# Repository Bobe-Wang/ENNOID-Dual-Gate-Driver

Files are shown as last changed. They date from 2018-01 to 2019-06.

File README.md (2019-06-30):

# ENNOID - Dual Gate Driver

The "Dual Gate Driver" can be directly connected to this control board:

https://github.com/paltatech/VESC-controller

The driver is pin compatible with several power modules such as the ones listed below:

- http://www.mitsubishielectric.com/semiconductors/content/product/powermod/powmod/igbtmod/tgatef/cm300du-12f_e.pdf
- https://www.wolfspeed.com/cas120m12bm2

## V0.1 (untested & archived):

V0.1 is based upon the design from wolfspeed two-channel gate driver for 1200V SiC MOSFET power modules
- https://www.wolfspeed.com/cgd15hb62p1

Feature:

- Dual gate driver
- 2W Isolated power supply / gate
- Direct mount low inductance design
- Short circuit protection
- Under voltage protection

Changes from the original wolfspeed design:

- Added Voltage sense circuit (Experimental)
- 98 x 60 mm 2 layer PCB made with Kicad
- Current sensor connector
- Temperature sensor circuit & connector
- Minimum SMD 0805 components size for easy handsoldering
- 2x8 (16) pins headers for easy connection with VESC board

## V0.2:

V0.2 is based upon the design from tiduc70a.pdf.

- http://www.ti.com/lit/ug/tiduc70a/tiduc70a.pdf

Changes from V0.1 include:

- BJT based powerstage instead of mosfet IC IXD-609
- Adjustable soft turnoff feature
- SMD gate resistor instead of MELF
- Active clamping / Over voltage protection
- Shoot trough EMI protection on PWM input

BOM link for 3 boards at Mouser below : 
- https://www.mouser.com/ProjectManager/ProjectDetail.aspx?AccessID=f6574b98ce

### Schematics

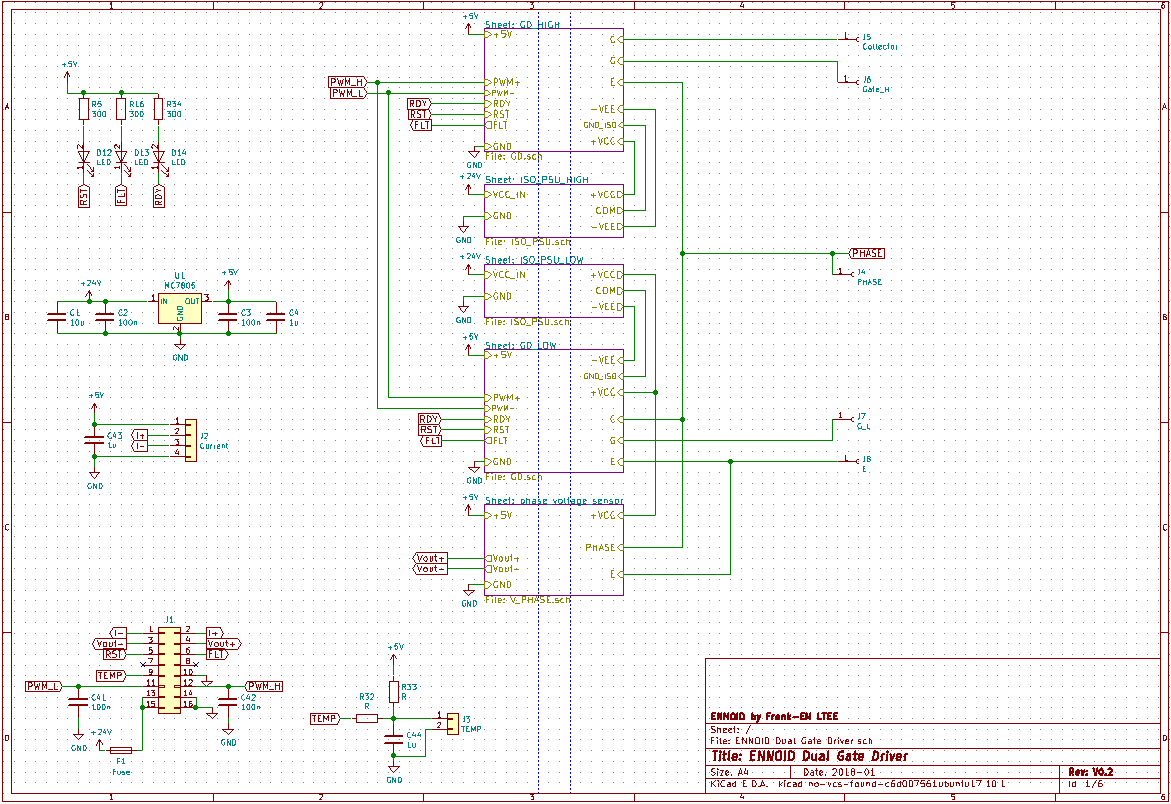
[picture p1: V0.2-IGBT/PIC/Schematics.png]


### Top View

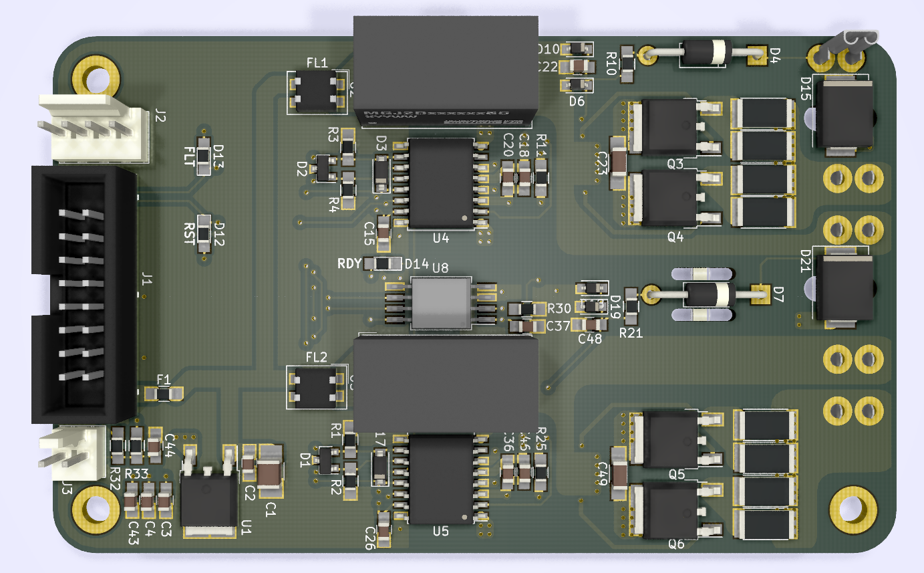
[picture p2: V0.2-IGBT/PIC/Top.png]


### Bottom View

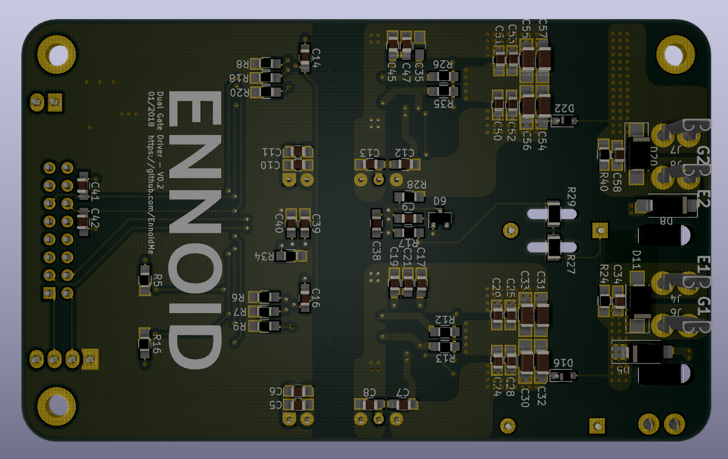
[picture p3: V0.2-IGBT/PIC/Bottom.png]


### Board View

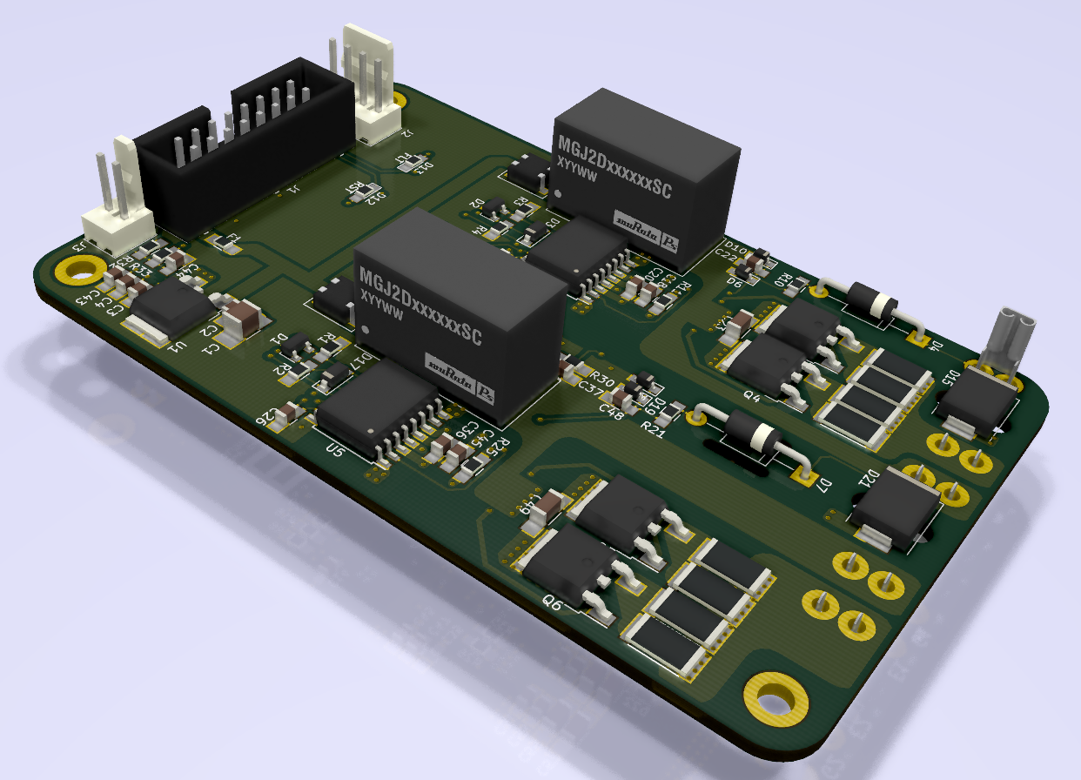
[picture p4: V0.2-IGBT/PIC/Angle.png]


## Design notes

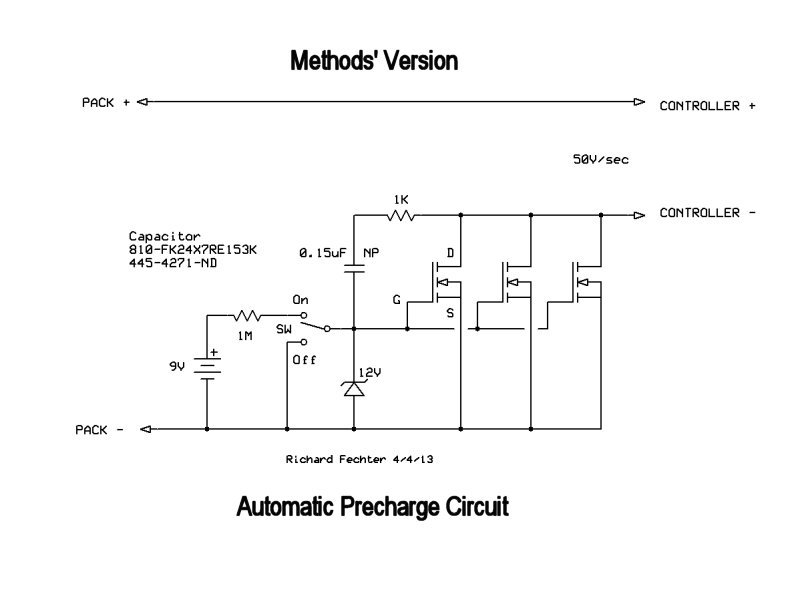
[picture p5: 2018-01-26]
VBUS-Sense/PCB/Automatic Precharge.jpg

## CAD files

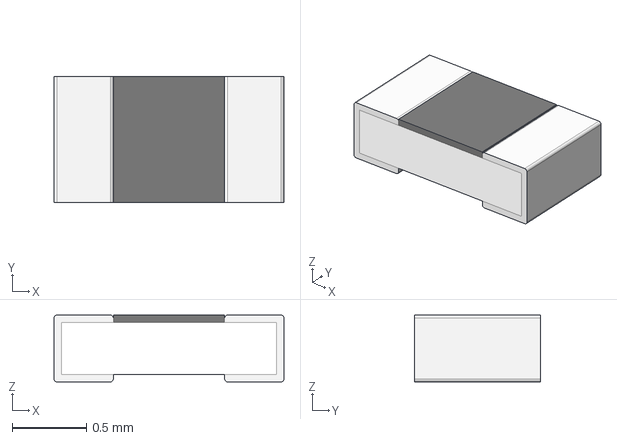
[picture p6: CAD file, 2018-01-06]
VBUS-Sense/3Dlib/r_0603_h078.step
1.55 x 0.85 x 0.45 mm

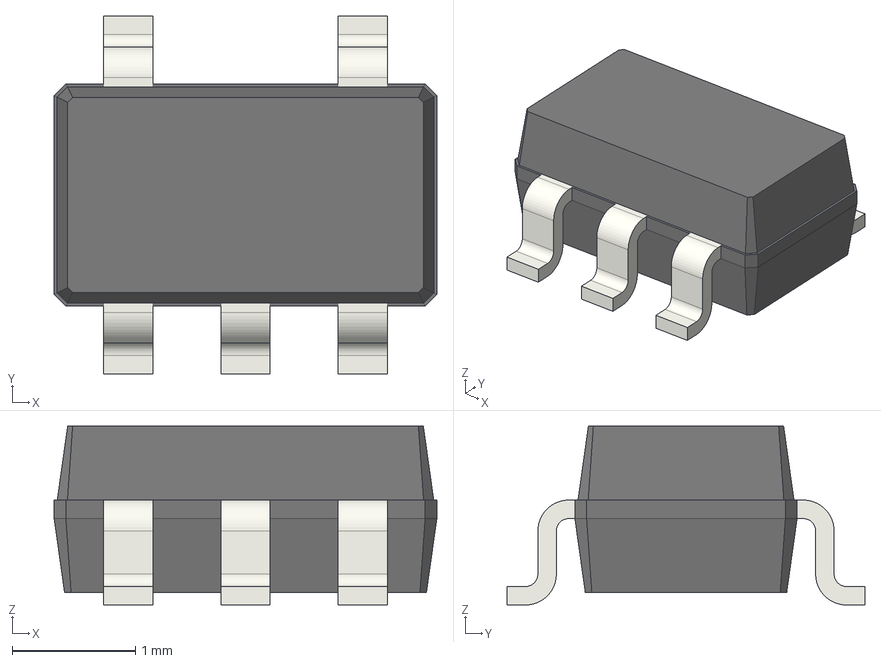
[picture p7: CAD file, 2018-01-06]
VBUS-Sense/3Dlib/sot23_5_18x29_p095.step
3.10 x 2.90 x 1.45 mm

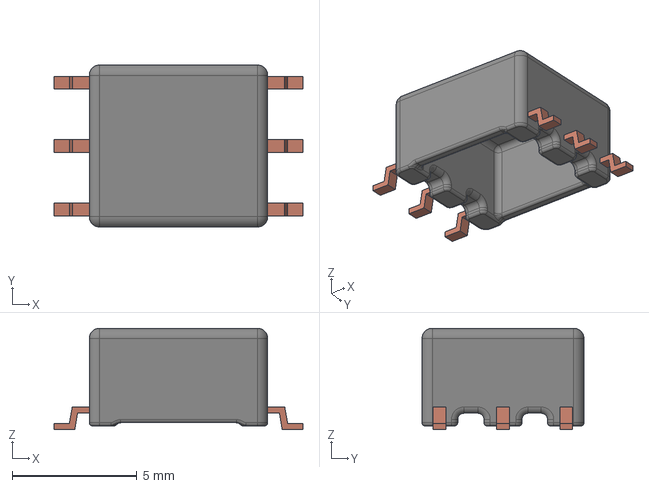
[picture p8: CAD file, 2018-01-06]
VBUS-Sense/3Dlib/250-1109-rev1.step
9.96 x 6.48 x 4.06 mm

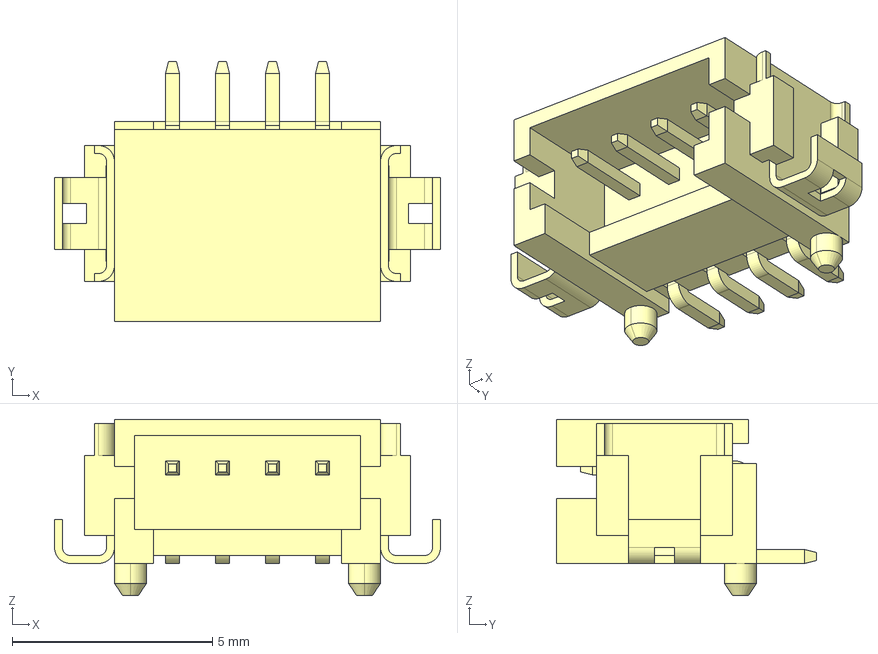
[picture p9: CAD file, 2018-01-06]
VBUS-Sense/3Dlib/DF13-4P-1.25H.stp
9.65 x 6.50 x 4.40 mm

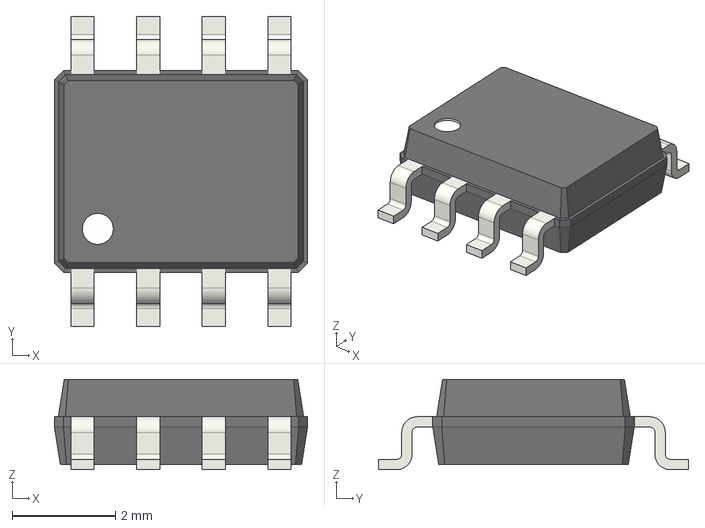
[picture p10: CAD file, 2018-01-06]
VBUS-Sense/3Dlib/soic_8_39x49_p127.step
4.90 x 6.00 x 1.75 mm

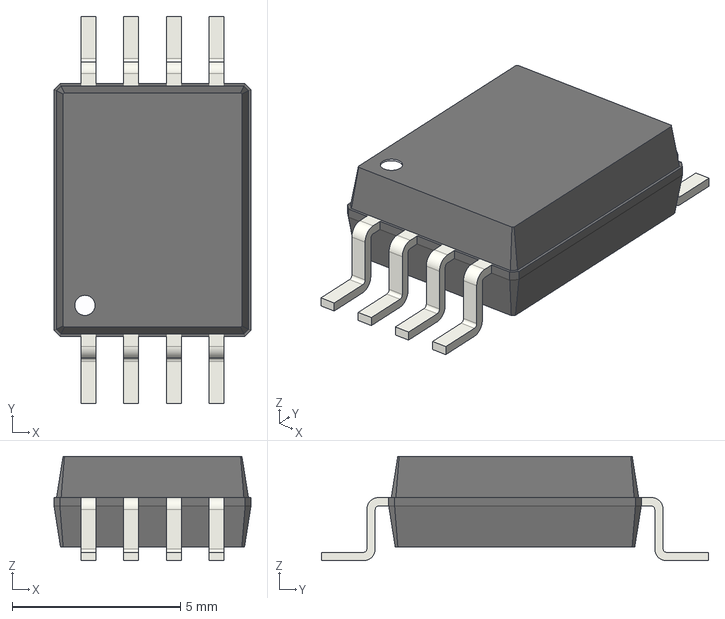
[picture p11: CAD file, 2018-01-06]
VBUS-Sense/3Dlib/soic_8_75x58_p127.step
5.85 x 11.5 x 3.10 mm

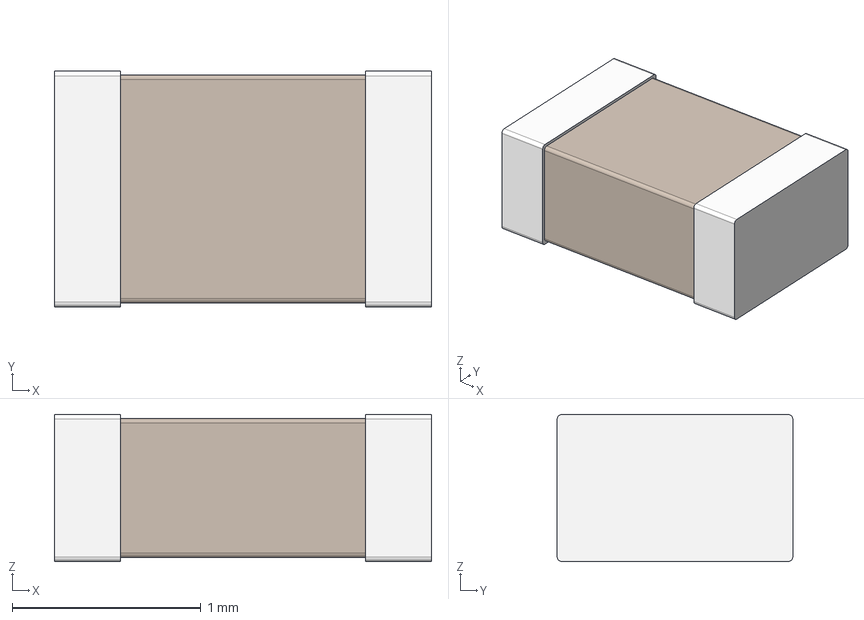
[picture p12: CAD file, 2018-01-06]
VBUS-Sense/3Dlib/c_0805_h078.step
2.00 x 1.25 x 0.78 mm

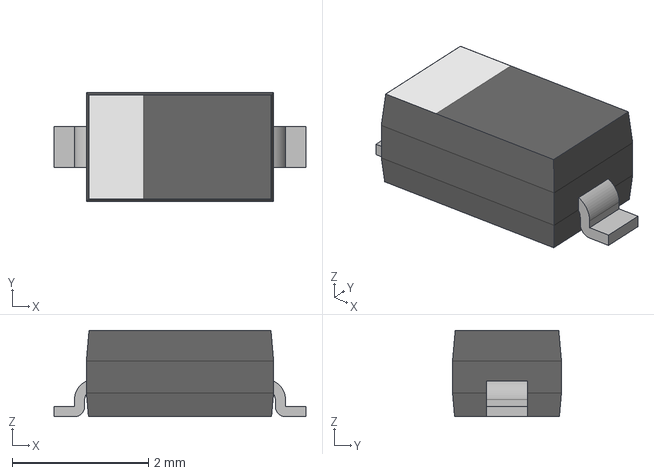
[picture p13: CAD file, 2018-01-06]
VBUS-Sense/3Dlib/SOD-123.step
3.70 x 1.60 x 1.27 mm

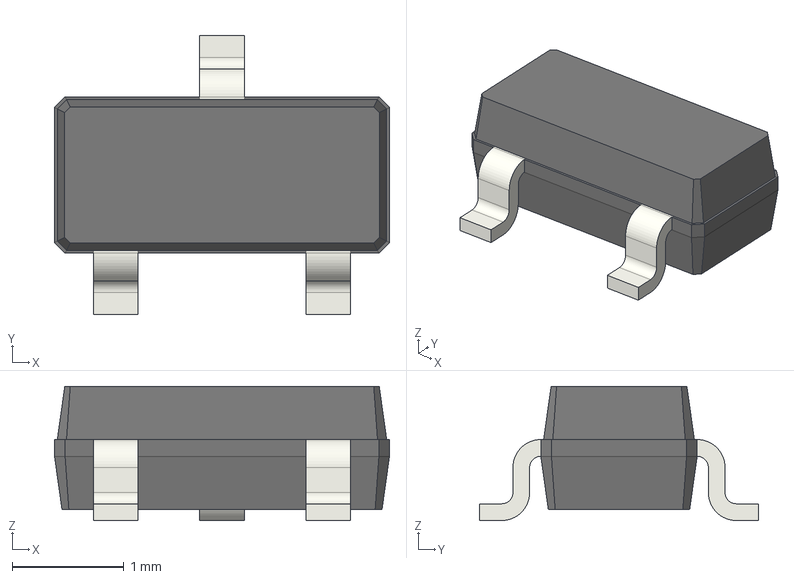
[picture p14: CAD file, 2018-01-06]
VBUS-Sense/3Dlib/sot23_3_25x30_p095.step
3.00 x 2.50 x 1.20 mm

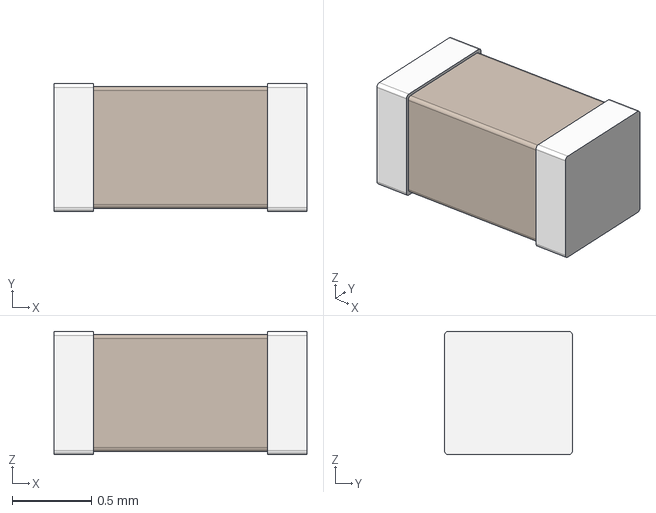
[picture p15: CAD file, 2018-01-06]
VBUS-Sense/3Dlib/c_0603_h078.step
1.60 x 0.81 x 0.78 mm

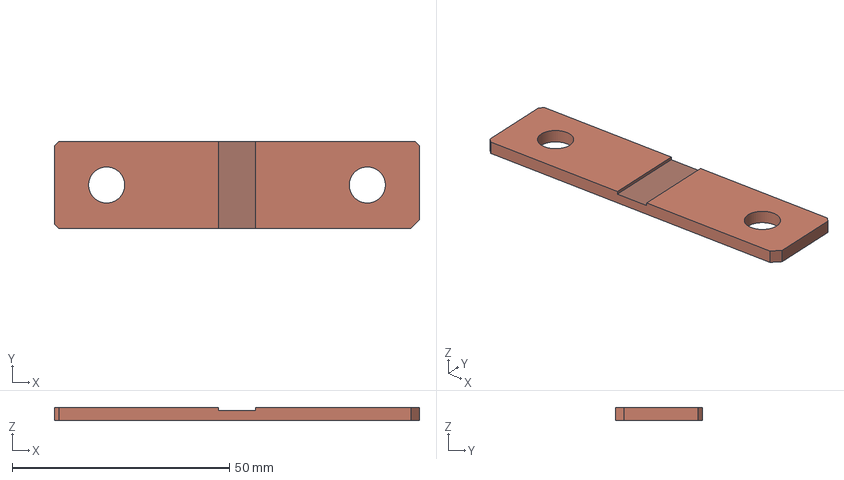
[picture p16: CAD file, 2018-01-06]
VBUS-Sense/3Dlib/BAS-M-R0002.step
84.0 x 20.0 x 3.00 mm

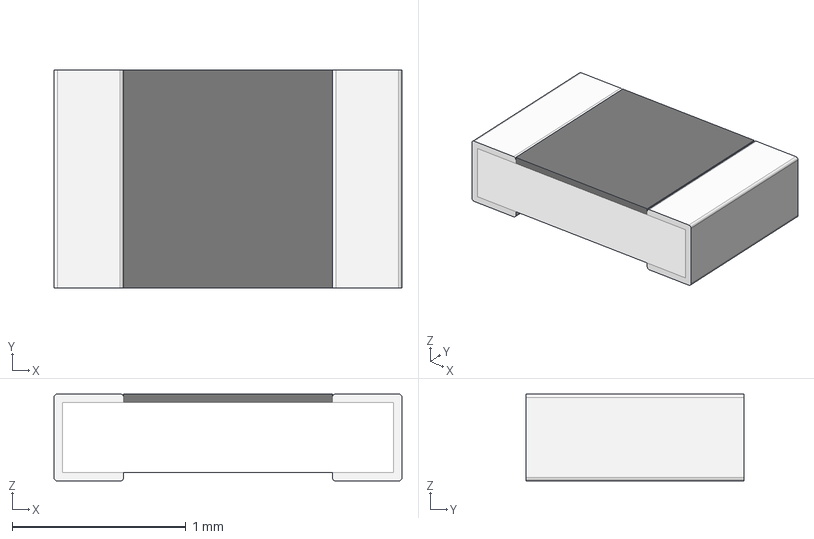
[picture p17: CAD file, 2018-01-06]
VBUS-Sense/3Dlib/r_0805_h078.step
2.00 x 1.25 x 0.5 mm

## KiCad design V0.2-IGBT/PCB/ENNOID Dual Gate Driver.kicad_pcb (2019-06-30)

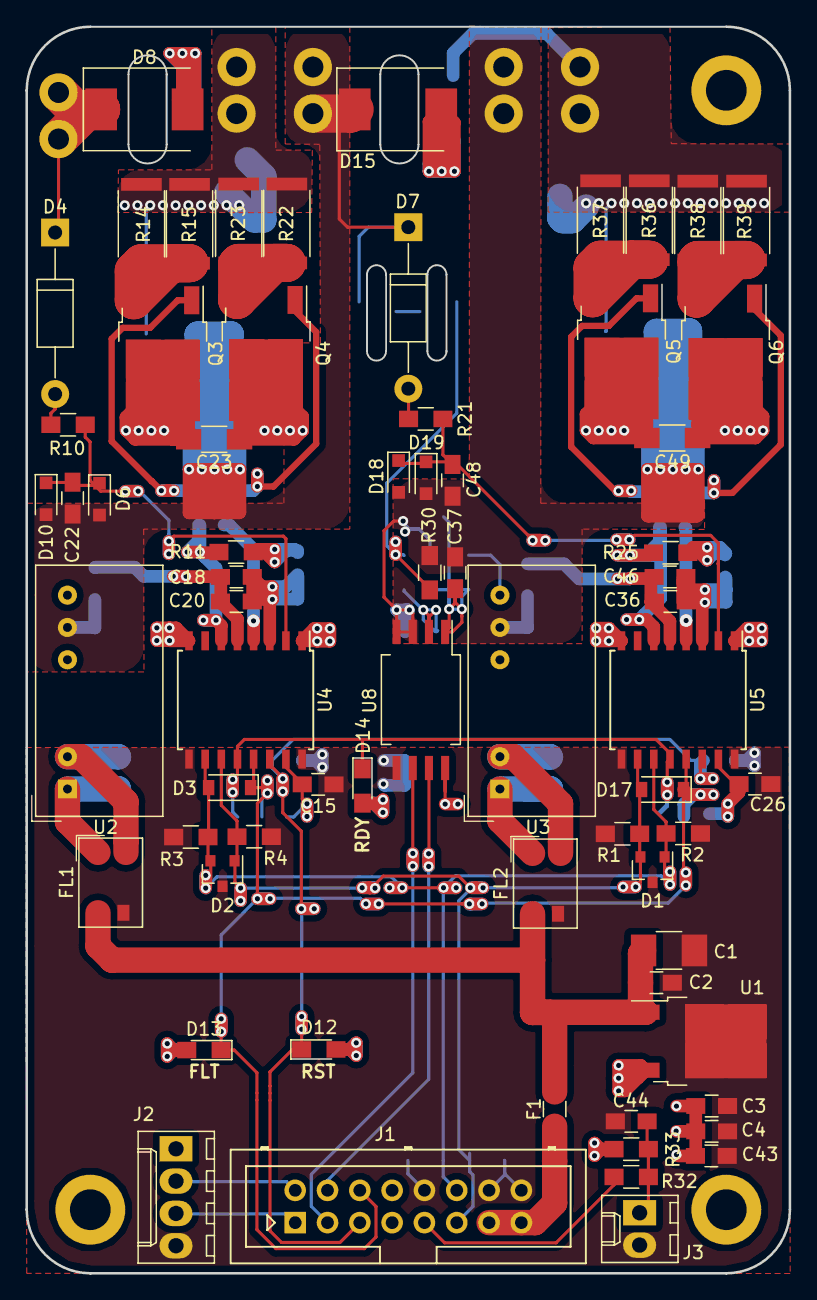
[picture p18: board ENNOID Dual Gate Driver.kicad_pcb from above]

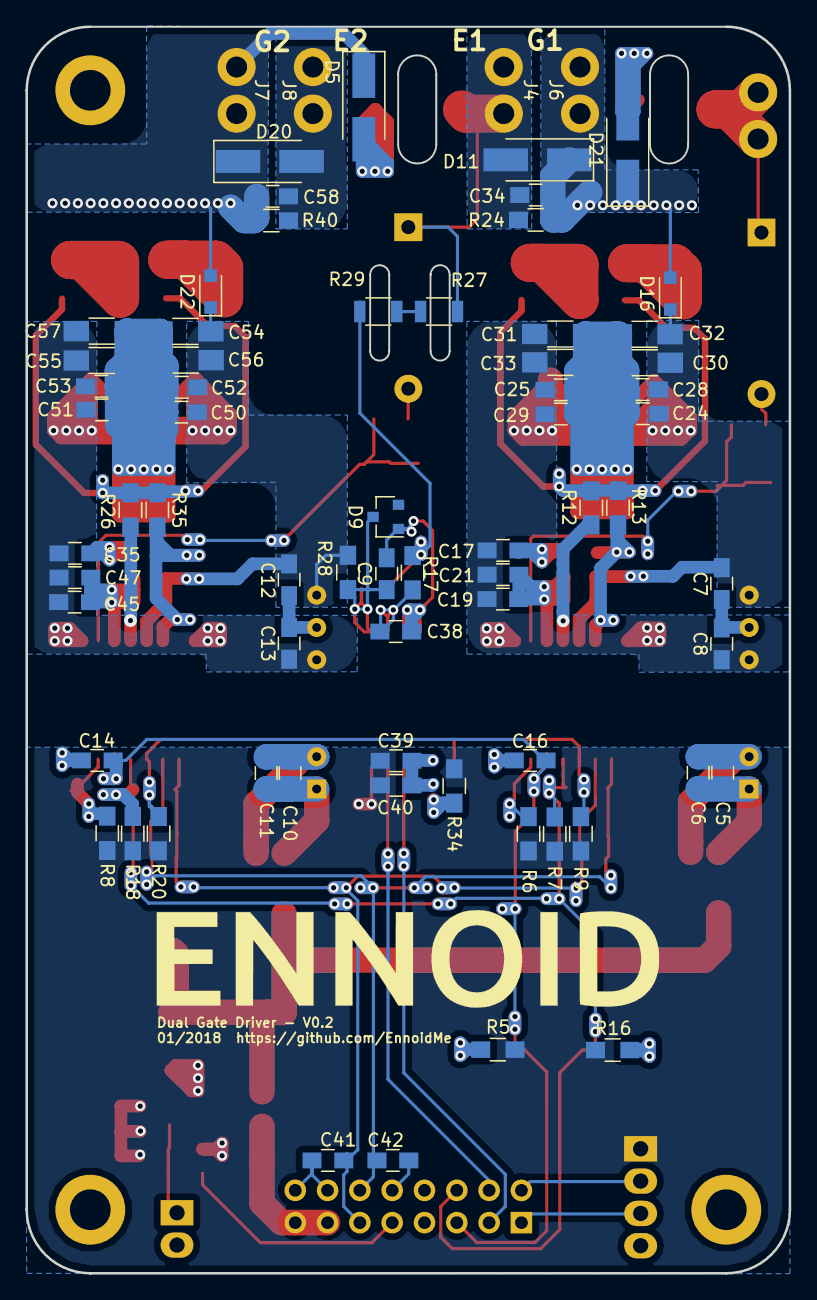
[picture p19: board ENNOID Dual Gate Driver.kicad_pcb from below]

Board: 2 copper layers, 60.0 x 98.0 mm, 142 parts (71 on the bottom side), 57 nets.

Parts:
C1: 10u; C_1210_HandSoldering
C2, C3, C5, C10, C14, C15, C16, C18, C19, C24, C25, C26, C36, C37, C39, C41, C42, C45, C50, C51: 100n; C_0805_HandSoldering
C4, C6, C7, C8, C11, C12, C13, C20, C21, C28, C29, C43, C44, C46, C47, C52, C53: 1u; C_0805_HandSoldering
C9: 10u; C_0805_HandSoldering
C17, C35: 15n; C_0805_HandSoldering
C22, C48: 220p; C_0805_HandSoldering
C23, C30, C31, C32, C33, C49, C54, C55, C56, C57: 10u; C_1206_HandSoldering
C34, C58: 0.22u; C_0805_HandSoldering
C38: 330p; C_0805_HandSoldering
C40: 2.2u; C_0805_HandSoldering
D1, D2: GSOT03C; SOT-23
D3, D17: 1N4148W; D_SOD-123
D4, D7: sTth112; D_DO-41_SOD81_P12.70mm_Horizontal
D5, D21: es2j-ltp; D_SMA_Handsoldering
D6, D18: MMSZ5242BS; D_SOD-323_HandSoldering
D8, D15: smcj440ca; D_SMC
D9: 5V; D_SOT-23_ANK
D10, D19: BAT54WS-7-F; D_SOD-323_HandSoldering
D11, D20: SMAJ18CA; D_SMA_Handsoldering
D12, D13, D14: LED; LED_0805_HandSoldering
D16, D22: PMEG4010; D_SOD-323_HandSoldering
F1: Fuse; R_0805_HandSoldering
FL1, FL2: ACM4520
G1: Logo_ENNOID; ENNOID-LOGO
J1: Conn_02x08_Odd_Even; Multicomp_MC9A12-1634_2x08x2.54mm_Straight
J2: Current; Molex_KK-6410-04_04x2.54mm_Straight
J3: TEMP; Molex_KK-6410-02_02x2.54mm_Straight
J4: PHASE; Quick_fit_terminal
J5: Collector; Quick_fit_terminal
J6: Gate_H; Quick_fit_terminal
J7: G_L; Quick_fit_terminal
J8: E; Quick_fit_terminal
J9: Mounting hole 1; MountingHole_3.2mm_M3_ISO14580_Pad
J10: Mounting Hole 2; MountingHole_3.2mm_M3_ISO14580_Pad
J11: Mounting Hole 3; MountingHole_3.2mm_M3_ISO14580_Pad
Q3, Q5: MJD3055T4G; TO-252-2
Q4, Q6: MJD2955T4G; TO-252-2
R1, R3: 4.7k; R_0805_HandSoldering
R2, R4, R10, R21, R30: 1k; R_0805_HandSoldering
R5, R16, R34: 300; R_0805_HandSoldering
R6, R8, R17: 10; R_0805_HandSoldering
R7, R9, R18, R20, R24, R40: 10k; R_0805_HandSoldering
R11, R12, R13, R25, R26, R35: 12; R_0805_HandSoldering
R14, R15, R22, R23, R36, R37, R38, R39: 3; R_2512
R27, R29: 1M; R_1206
R28: 800; R_0805_HandSoldering
R32, R33: R; R_0805_HandSoldering
U1: MC7805; TO-252-2
U2, U3: MGJ2; DCDC-Conv_muRata_MGJ2
U4, U5: ISO5852SDWR; SOIC-16W_7.5x10.3mm_Pitch1.27mm
U8: AMC1301; SSO-8_6.8x5.9mm_Pitch1.27mm_Clearance8mm

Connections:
+5V: C3.1, C4.1, C39.1, C40.1, C43.1, J2.1, R5.1, R6.2, R7.1, R8.2, R9.1, R16.1, R18.1, R20.1, R33.1, R34.1, U1.3, U8.8
+24V: C1.1, C2.1, F1.2, FL1.1, FL2.1, U1.1
/GD_HIGH/+VCC: C7.1, C18.1, C20.1, C23.1, C24.1, C28.1, C30.1, C32.1, D16.1, Q3.2, U2.7, U4.5
/GD_HIGH/-VEE: C8.2, C17.2, C19.2, C21.2, C23.2, C25.2, C29.2, C31.2, C33.2, Q4.2, U2.5, U4.1, U4.8
/GD_HIGH/C: D4.1, D8.1, J5.1
/GD_HIGH/G: C34.1, D11.1, D16.2, D21.1, J6.1, R14.1, R15.1, R22.1, R23.1, R24.2
/GD_LOW/+VCC: C12.1, C36.1, C46.1, C49.1, C50.1, C52.1, C54.1, C56.1, D22.1, Q5.2, R28.2, U3.7, U5.5
/GD_LOW/-VEE: C13.2, C35.2, C45.2, C47.2, C49.2, C51.2, C53.2, C55.2, C57.2, Q6.2, U3.5, U5.1, U5.8
/GD_LOW/G: C58.1, D5.1, D20.1, D22.2, J7.1, R36.1, R37.1, R38.1, R39.1, R40.2
/ISO_PSU_LOW/COM: C9.2, C12.2, C13.1, C37.2, C38.2, C48.2, C50.2, C51.1, C52.2, C53.1, C54.2, C55.1, C56.2, C57.1, C58.2, D9.2, D18.2, D19.2, D20.2, J8.1, R30.1, R40.1, U3.6, U8.3, U8.4
FLT: D3.1, D13.1, D17.1, J1.6, R7.2, R18.2, U4.13, U5.13
GND: C1.2, C2.2, C3.2, C4.2, C14.2, C15.1, C16.2, C26.1, C39.2, C40.2, C41.2, C42.2, C43.2, C44.2, D1.3, D2.3, FL1.2, FL2.2, J1.10, J1.14, J1.16, J2.4, J3.2, R1.2, R2.2, R3.2, R4.2, U1.2, U4.9, U4.16, U5.9, U5.16, U8.5
I+: J1.2, J2.2
I-: J1.1, J2.3
unnamed: C5.1, C6.1, FL1.4, U2.1
unnamed: C5.2, C6.2, FL1.3, U2.2
unnamed: C10.1, C11.1, FL2.4, U3.1
unnamed: C10.2, C11.2, FL2.3, U3.2
unnamed: C15.2, R6.1, U4.15
unnamed: C17.1, R11.1
unnamed: C18.2, C19.1, C20.2, C21.1, U4.3
unnamed: C22.1, D6.1, D10.1, R10.2, U4.2
unnamed: C26.2, R8.1, U5.15
unnamed: C35.1, R25.1
unnamed: C36.2, C45.1, C46.2, C47.1, U5.3
unnamed: C9.1, C37.1, D9.1, R28.1, U8.1
unnamed: C38.1, R17.2, U8.2
unnamed: C44.1, J3.1, R32.1, R33.2
unnamed: C48.1, D18.1, D19.1, R21.2, U5.2
unnamed: D4.2, R10.1
unnamed: D7.2, R21.1
unnamed: D12.2, R5.2
unnamed: D13.2, R16.2
unnamed: D14.2, R34.2
unnamed: D5.2, D15.2
unnamed: D8.2, D21.2
unnamed: F1.1, J1.13, J1.15
unnamed: Q3.1, Q4.1, R12.1, R13.1
unnamed: Q3.3, R14.2, R15.2
unnamed: Q4.3, R22.2, R23.2
unnamed: Q5.1, Q6.1, R26.1, R35.1
unnamed: Q5.3, R36.2, R37.2
unnamed: Q6.3, R38.2, R39.2
unnamed: R11.2, R13.2, U4.6
unnamed: R12.2, U4.4
unnamed: R17.1, R29.1, R30.2
unnamed: R25.2, R35.2, U5.6
unnamed: R26.2, U5.4
unnamed: R27.1, R29.2
PHASE: C7.2, C8.1, C22.2, C24.2, C25.1, C28.2, C29.1, C30.2, C31.1, C32.2, C33.1, C34.2, D6.2, D7.1, D10.2, D11.2, D15.1, J4.1, R24.1, R27.2, U2.6
PWM_H: C42.1, D1.1, D2.2, D3.2, J1.12, R2.1, R3.1, U4.10, U5.11
PWM_L: C41.1, D1.2, D2.1, D17.2, J1.11, R1.1, R4.1, U4.11, U5.10
RDY: D14.1, R9.2, R20.2, U4.12, U5.12
RST: C14.1, C16.1, D12.1, J1.5, U4.14, U5.14
TEMP: J1.9, R32.2
Vout+: J1.4, U8.7
Vout-: J1.3, U8.6

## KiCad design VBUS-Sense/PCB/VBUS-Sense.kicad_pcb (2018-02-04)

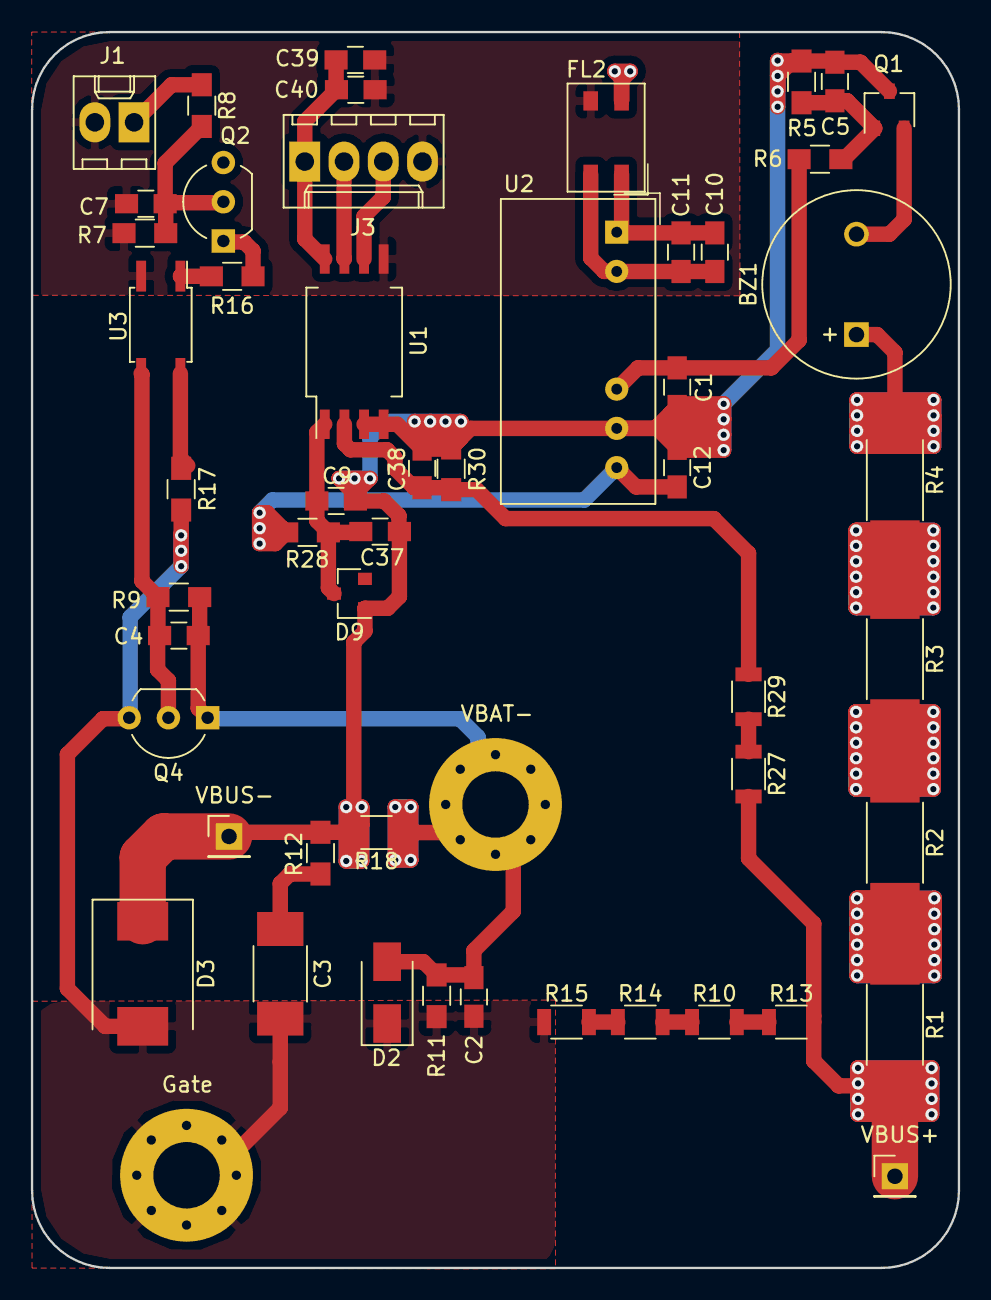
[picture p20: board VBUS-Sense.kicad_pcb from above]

Board: 2 copper layers, 60.0 x 80.0 mm, 54 parts (1 on the bottom side), 31 nets.

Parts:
BZ1: Buzzer; MagneticBuzzer_ProSignal_ABT-410-RC
C1, C11, C12: 1u; C_0805_HandSoldering
C2: 0.15u; C_0805_HandSoldering
C3: 0.15u; C_1812_HandSoldering
C4, C5, C7, C10, C37, C39: 100n; C_0805_HandSoldering
C9: 10u; C_0805_HandSoldering
C38: 330p; C_0805_HandSoldering
C40: 2.2u; C_0805_HandSoldering
D2: D_Zener 18V SMAJ18CA; D_SMA
D3: D_Zener 440v SMJC440CA; D_SMC
D9: 5V; D_SOT-23_ANK
FL2: ACM4520
J1: Conn_01x02 to external 12V power switch or VESC G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; Molex_KK-6410-02_02x2.54mm_Straight
J3: Conn_01x04 to vesc board; Molex_KK-6410-04_04x2.54mm_Straight
LOGO1: Logo_ENNOID; ENNOID-LOGO
MK1: VBUS-; Pin_Header_Straight_1x01_Pitch2.54mm
MK2: VBUS+; Pin_Header_Straight_1x01_Pitch2.54mm
MK3: Gate; MountingHole_4.3mm_M4_Pad_Via
MK4: VBAT-; MountingHole_4.3mm_M4_Pad_Via
Q1: Depletion mode FET ex: CPC3982; SOT-23W
Q2, Q4: 2N7000; TO-92_Inline_Wide
R1, R2, R3, R4: 7.5K; R_2512_HandSoldering
R5: 20k; R_0805_HandSoldering
R6: 100; R_0805_HandSoldering
R7: 1M; R_0805_HandSoldering
R8, R12, R16, R17, R30: 1k; R_0805_HandSoldering
R9: 10k; R_0805_HandSoldering
R10, R13, R14, R15, R18: 200k; R_1206
R11: 30k; R_0805_HandSoldering
R27, R29: 1M; R_1206
R28: 800; R_0805_HandSoldering
U1: AMC1301; SSO-8_6.8x5.9mm_Pitch1.27mm_Clearance8mm
U2: MGJ2; DCDC-Conv_muRata_MGJ2
U3: LTV-356T; SO-4_4.4x3.6mm_Pitch2.54mm

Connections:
+5V: C39.1, C40.1, FL2.1, J3.1, Q2.3, U1.8
/ISO_PSU/+VCC: C12.1, R28.2, U2.7
/ISO_PSU/-VEE: C1.2, R6.2, U2.5
/ISO_PSU/COM: C1.1, C5.2, C9.2, C12.2, C37.2, C38.2, D3.1, D9.2, MK1.1, Q1.3, R5.1, R12.1, R18.2, R30.1, U1.3, U1.4, U2.6
/Inrush_Limiter/+VBUS: MK2.1, R1.2, R13.2, R27.2
/Inrush_Limiter/GATE: C2.1, C3.2, D2.1, D3.2, MK3.1, Q4.3, R11.2, R15.1, R17.2
/Inrush_Limiter/ON/OFF: J1.1, R8.2
/Inrush_Limiter/VBAT-: C2.2, C4.2, D2.2, MK4.1, Q4.1, R9.1, R11.1, R18.1
/V_BUS/Vout+: J3.2, U1.7
/V_BUS/Vout-: J3.3, U1.6
GND: C7.2, C39.2, C40.2, FL2.2, J1.2, J3.4, R7.2, U1.5, U3.2
unnamed: BZ1.1, R4.1
unnamed: BZ1.2, Q1.2
unnamed: C3.1, R12.2
unnamed: C4.1, Q4.2, R9.2, U3.3
unnamed: C5.1, Q1.1, R5.2, R6.1
unnamed: C7.1, Q2.2, R7.1, R8.1
unnamed: C10.1, C11.1, FL2.4, U2.1
unnamed: C10.2, C11.2, FL2.3, U2.2
unnamed: C9.1, C37.1, D9.1, R28.1, U1.1
unnamed: C38.1, R29.1, R30.2, U1.2
unnamed: Q2.1, R16.2
unnamed: R1.1, R2.2
unnamed: R2.1, R3.2
unnamed: R3.1, R4.2
unnamed: R10.1, R14.2
unnamed: R10.2, R13.1
unnamed: R14.1, R15.2
unnamed: R16.1, U3.1
unnamed: R17.1, U3.4
unnamed: R27.1, R29.2

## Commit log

2017-12-13 Gate power calcculation
    [Gate Power calculator.ods]
2017-12-13 Update removing .bak & V_phase adj submodule
    [ENNOID Dual Gate Driver.sch, GD.sch, Gate Power calculator.ods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]
2017-12-13 .gitignore for kicad
    [GD.sch]
2017-12-14 Schematics & footprints completed
    Ready for PCBnew
    [ENNOID Dual Gate Driver.kicad_pcb, ENNOID Dual Gate Driver.sch, Fault_LED.sch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]
2017-12-14 PCB half-done
    [ENNOID Dual Gate Driver.kicad_pcb, ENNOID Dual Gate Driver.sch, GD.sch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]
2017-12-16 Routing has started
    [ENNOID Dual Gate Driver.kicad_pcb, ENNOID Dual Gate Driver.sch, GD.sch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]
2017-12-18 PCB completed with readme update
    [ACM4520.fcstd, ACM4520.step, AMC1301.fcstd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]
2017-12-18 Minor updates
    [ENNOID Dual Gate Driver.kicad_pcb, ENNOID Dual Gate Driver.sch]
2017-12-18 Minor changes
    [ENNOID Dual Gate Driver.kicad_pcb, GD.sch]
2017-12-18 Small changes
    [ENNOID Dual Gate Driver.kicad_pcb, MGJ2.step, mgj2.step]
2017-12-18 pcb error correction
    [ENNOID Dual Gate Driver.kicad_pcb, ENNOID Dual Gate Driver.sch, _saved_GD.sch]
2017-12-18 Small updates
    [GD.sch, _saved_GD.sch]
2017-12-19 PCB changes
    [ENNOID Dual Gate Driver-B.Cu.gbl, ENNOID Dual Gate Driver-B.Mask.gbs, ENNOID Dual Gate Driver-B.SilkS.gbo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]
2017-12-27 V0.1 wolfspeed
    [ACM4520.fcstd, ACM4520.step, AMC1301.fcstd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]
2017-12-27 V0.2 readme
    [BOM CGD15HB62P1 AB.ods]
2017-12-28 v0.2 PCB
    [ENNOID Dual Gate Driver.kicad_pcb, ENNOID Dual Gate Driver.sch, GD.sch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]
2018-01-01 v0.2 PCB POWER STAGE COMPLETED
    [ENNOID Dual Gate Driver.kicad_pcb, _saved_ENNOID Dual Gate Driver.sch, _saved_GD.sch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]
2018-01-02 v2.0 PCB SIGNAL SIDE
    [ENNOID Dual Gate Driver.kicad_pcb, ENNOID Dual Gate Driver.sch, GD.sch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]
2018-01-02 SIGNAL PCV V0.2
    [ENNOID Dual Gate Driver.kicad_pcb]
2018-01-02 V0.2 PCB completed
    [ENNOID Dual Gate Driver.kicad_pcb]
2018-01-03 V0.2 completed
    [ENNOID Dual Gate Driver-B.Cu.gbl, ENNOID Dual Gate Driver-B.Mask.gbs, ENNOID Dual Gate Driver-B.SilkS.gbo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]
2018-01-03 PCB V0.2
    [ENNOID Dual Gate Driver.kicad_pcb]
2018-01-03 ENNOID LOGO on V0.2
    [ENNOID Dual Gate Driver.kicad_pcb]
2018-01-04 V0.2 shoot through EMI protection added
    In response to Marcos repply to my post on endless sphere https://endless-sphere.com/forums/viewtopic.php?f=30&t=89056&start=75
    [ENNOID Dual Gate Driver-B.Cu.gbl, ENNOID Dual Gate Driver-B.Mask.gbs, ENNOID Dual Gate Driver-B.SilkS.gbo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]
2018-01-04 V0.2 Fab files
    [ENNOID Dual Gate Driver-B.Cu.gbl, ENNOID Dual Gate Driver-B.Mask.gbs, ENNOID Dual Gate Driver-B.SilkS.gbo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]
2018-01-06 VBUS sensor & voltage sense circuit changes
    [250-1109-rev1.step, BAS-M-R0002.step, DF13-4P-1.25H.stp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]
2018-01-08 Schematics update
    [ENNOID Dual Gate Driver.kicad_pcb, ENNOID Dual Gate Driver.sch, GD.sch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]
2018-01-08 V0.2 BOM and schematics updated
    [ENNOID Dual Gate Driver.kicad_pcb, ENNOID Dual Gate Driver.sch, GD.sch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]
2018-01-08 V0.2 BOM and schematics updates
2018-01-08 V0.2 pcb changes
    [ENNOID Dual Gate Driver.kicad_pcb, GD.sch, ISO_PSU.sch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]
2018-01-09 V0.2 pics update
    [ENNOID Dual Gate Driver.kicad_pcb]
2018-01-10 V0.3 started
    [ACM4520.fcstd, ACM4520.step, AMC1301.fcstd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]
2018-01-15 removed v0.3
    [ACM4520.fcstd, ACM4520.step, AMC1301.fcstd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]
2018-01-21 Maintenance update
    [ENNOID Dual Gate Driver.kicad_pcb, ENNOID Dual Gate Driver.sch, GD.sch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]
2018-01-26 VBUS update
    [ENNOID Dual Gate Driver.kicad_pcb, ISO_PSU.sch, Inrush_Limiter.sch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]
2018-01-26 PIC update
    [ENNOID Dual Gate Driver.kicad_pcb]
2018-01-26 BOM update
2018-01-26 VBUS-SENSE changes
    [ISO_PSU.sch, Inrush_Limiter.sch, VBUS-Sense.kicad_pcb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]
2018-01-27 VBUS sense
    [VBUS-Sense.sch]
2018-02-05 V0.3 - New voltage clamping technique
    Added TM4 reflex active clampiing
    [ENNOID Dual Gate Driver.kicad_pcb, ENNOID Dual Gate Driver.sch, GD.sch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]
2018-02-16 Readme update
    [ENNOID Dual Gate Driver.kicad_pcb, ENNOID Dual Gate Driver.sch, GD.sch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]
2019-04-08 no changes
    [ENNOID Dual Gate Driver.kicad_pcb, ENNOID Dual Gate Driver.sch, GD.sch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]
2019-06-30 Readme update no changes
    [ENNOID Dual Gate Driver.kicad_pcb]

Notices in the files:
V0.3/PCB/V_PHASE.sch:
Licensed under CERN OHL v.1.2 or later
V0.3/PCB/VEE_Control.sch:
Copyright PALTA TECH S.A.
